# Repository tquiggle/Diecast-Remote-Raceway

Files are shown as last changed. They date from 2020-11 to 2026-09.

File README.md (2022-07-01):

# Diecast-Remote-Raceway
The Diecast Remote Raceway (DRR) allows participants to race 1:64 scale die-cast cars (such as the popular Hot Wheels® cars from 
[Mattel](https://www.mattel.com/en-us)), head-to-head, from remote locations.  A DRR consists of an automated Starting Gate, an electronic Finish Line, and a web service that coordinates races between multiple raceways via the internet.

The DRR is comprised of three components:

* The Starting Gate that manages races on a single track.  The Starting Gate houses a Raspberry Pi Zero W single board computer that performs all local race operations. Reflective infrared track sensors plug into the Starting Gate to signal the presence of a car positioned in each starting location.  A race begins when cars are present in all lanes.  The Starting Gate connects via Bluetoot to the Finish Line that reports when cars finish a race.
* The Finish Line houses an ESP32 Arduino dev board that reports when a car passes over a sensor in each lane.
* The Coordinator is a Node.js application that coordinates the actions of multiple tracks competing against each other.  Each track signals when all lanes have cars ready to race.  When all tracks are ready, the Coordinator signals all tracks to start the local race.  Tracks report the elapsed time for each lane back to the coordinator, which then computes the overall race standings and returns the results to each track to display the race results.

## Operation

Start by mounting the Starting Gate onto a suitable elevated surface. The mount on the bottom of
the Starting Gate can be attached to a [Hot Wheels Clamp
3-way](https://www.thingiverse.com/thing:4037458) to clamp onto a chair, desk, shelf or other
surface.  Alternatively, you can attach to a photography tripod using a [Hot Wheels Track Tripod Connector ](https://www.thingiverse.com/thing:4376073).

Next, attach track sections to build a track of your liking.  Terminate the track with the Finish
Line component.

Apply power to both the Starting Gate and Finish Line using 5 Volt sources
and mini-USB cables.  Most phone chargers or power packs work well to
provide power.  When the Starting Gate has completed its initialization,
the display should look like this:

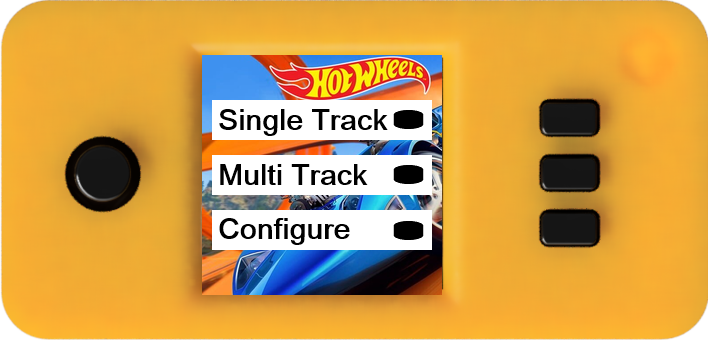
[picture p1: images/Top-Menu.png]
Top Menu


* To race locally, push the top button next to "Single Track"
* To race against another track, push the middle button next to "Multi Track"
* To set configuration parameters such as selecting car icons, other tracks to race against, tack timeout or WiFi parameters, push the button next to "Configure"

Once a race mode has been selected (Single Track or Multi Track) the
Starting Gate will establish a Bluetooth connection to the Finish Line.
This may take a minute or more to complete, during which time the
following is displayed:

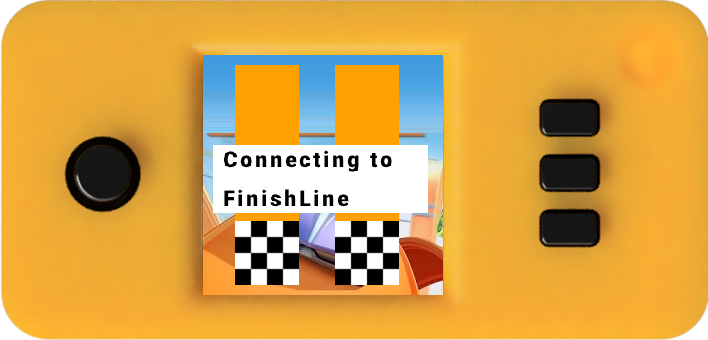
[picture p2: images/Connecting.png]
Connecting


### Multi-Track Race

In a multi-track race was selected, the Starting Gate contacts the race controller to await
another participating track.  The following is displayed:

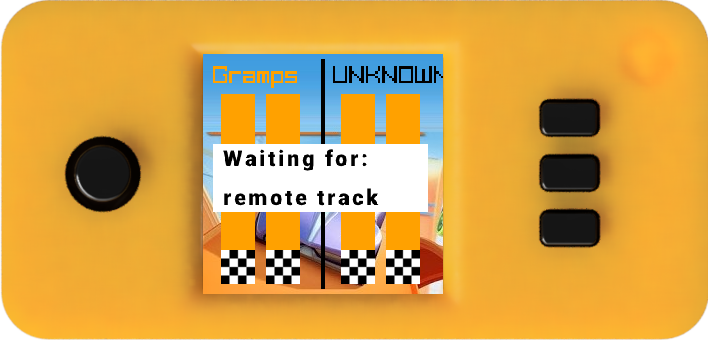
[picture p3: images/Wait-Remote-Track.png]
Wait Remote Track


Upon return, the name of the remote track is displayed
and the Starting Gate awaits cars in each starting gate.

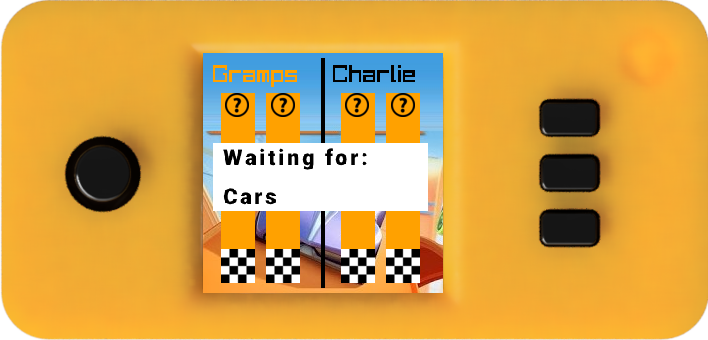
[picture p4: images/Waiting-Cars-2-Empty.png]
Waiting Cars 2


When a lane's sensor detects that a car has been placed in a lane, the "no
car" icon is replaced with the user's selected icon for that lane:

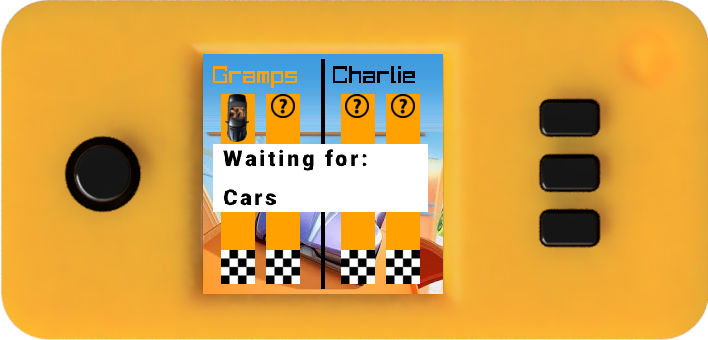
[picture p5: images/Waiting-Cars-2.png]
Waiting Cars 2


Once cars are present in all lanes of the local track the Starting Gate
contacts the race coordinator to signal that the track is ready to race and wait until the
remote track is also ready:

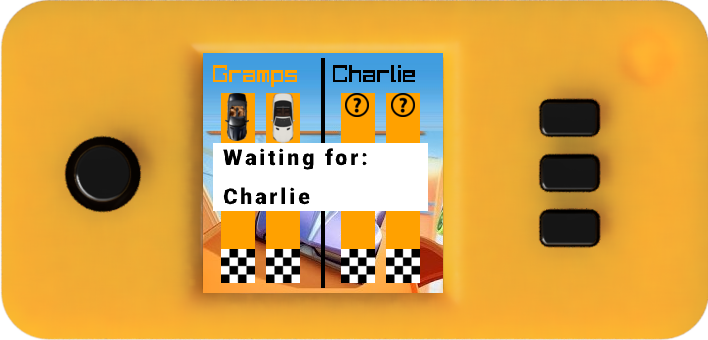
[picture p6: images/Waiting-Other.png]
Waiting on Other Track


Once both tracks are ready, there is a 3 second countdown and the
race begins.  The elapsed time is displayed as the race progresses,
and the icons travel down the image of the track.

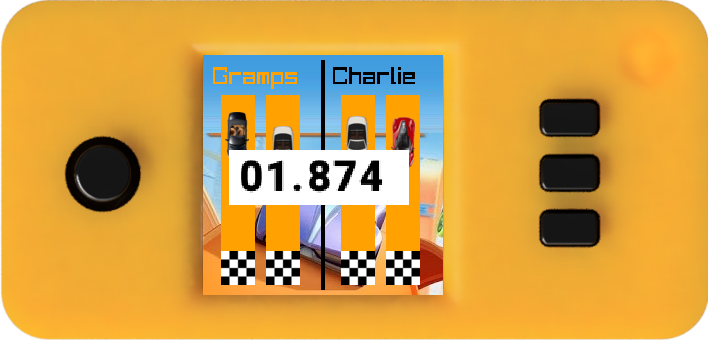
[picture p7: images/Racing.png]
Racing


Finally, when all cars have finished (or the configured timeout is reached) the results of the
race are displayed:

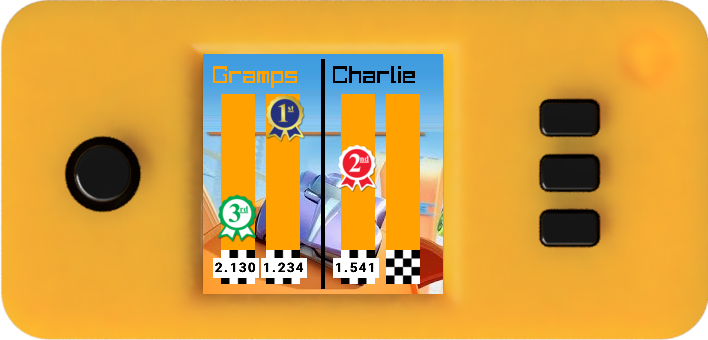
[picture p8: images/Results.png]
Results


and the starting gate barrier is raised to accept cars again.

To start next race, simply placing cars in the gates.  When the first car is placed, the
display clears the race results and goes back to the "Waiting for cars" state and the next race
proceeds.

### Single-Track Race

A Single Track race proceedes much like a Mulit Track but without the coordination with the
second track.  As soon as the connection to the Finish Line is established, the Starting Gate
waits for cars on the local track.

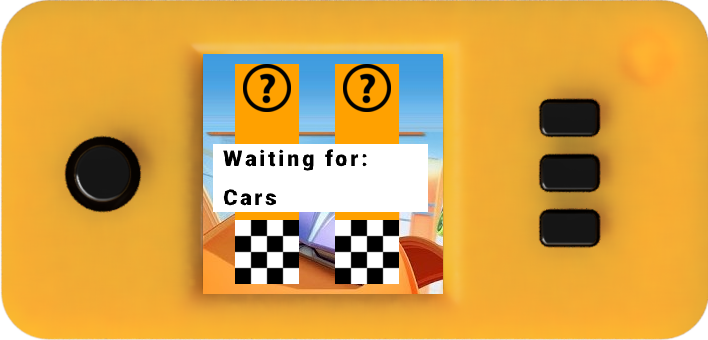
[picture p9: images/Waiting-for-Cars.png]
Waiting for Cars


When a lane's sensor detects that a car has been placed in a lane, the "no
car" icon is replaced with the user's selected icon for that lane:

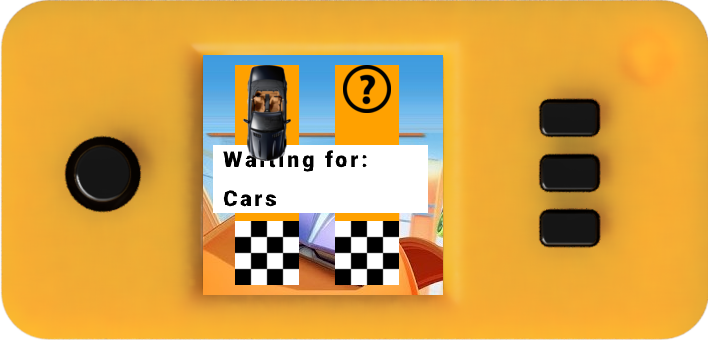
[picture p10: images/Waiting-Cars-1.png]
Waiting with 1 Car


Once all cars are present, there is a 3 second countdown and the race begins.

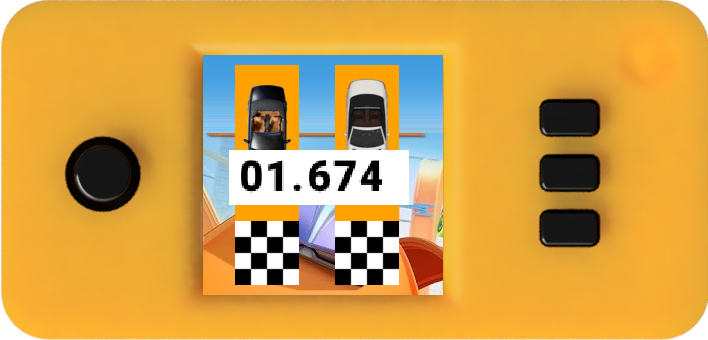
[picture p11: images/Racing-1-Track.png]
Racing 1 Track


When the race completes, the results are displayed:

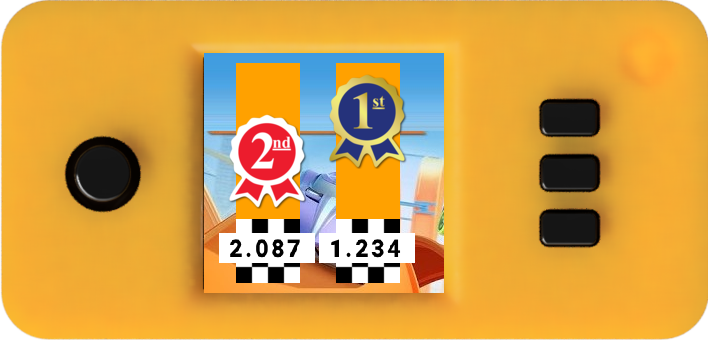
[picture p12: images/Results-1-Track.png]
Racing 1 Track


and the starting gate barrier is raised to accept cars again.

To start next race, simply placing cars in the gates.  When the first car is placed, the
display clears the race results and goes back to the "Waiting for cars" state and the next race
proceeds.

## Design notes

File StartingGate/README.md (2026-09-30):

# Diecast Remote Raceway - Starting Gate

This directory contains the 3D models, software and instructions for the Starting Gate component of the Diecast Remote Raceway.

Starting Gate

## 3D Printed Components

### Starting Gate

The Starting Gate is derived from the excellent design by 
[capsurfer](https://www.thingiverse.com/capsurfer/designs) on 
[Thingiverse](https://www.thingiverse.com/thing:4026846) with a number of modifications to adapt it to automation.

The following components are printed exactly as-is from capsurfer's original design:

* connector_v2.stl
* lever.stl
* lid.stl
* starter.stl
* thestick[\_long4].stl

As they are capsurfer's unmodified designs, I have not included the STL files in this
repository.  You will need to download those STLs from thingiverse.

The following components have been modified to suit automation

* open-box.stl - a modified version of box.stl to insert the track with a mounted sensor from the back of the box. The sensor would collide with the starter if inserted from the front.
* open-box-servo.stl - a modified version of open-box.stl for Lane 1 with an opening and mounting holes for a MG90S servo.
* sensor-track.stl - a modified version of track.stl designed to mount a [TCRT5000 Infrared Reflective Sensor Module](https://www.amazon.com/gp/product/B081RPJ44L) to detect the presence of a car.

* sensor-track-flush.stl - a modified version of sensor-track.stl that moves the sensor forward about 10mm.  Requires reworking the TCRT5000 sensors. See note below.
* servo-knob.stl - Modified version of knob.stl to make the arm much narrower and add holes for the servo control.
* lane-#.stl - modified versions of sensor-track-flush.stl with embossed lane numbers

I also moved the location of the track extrusions that accept the threaded heat set screw inserts further away from the track surface to
eliminate bulging of the track surface. This required changes to both the open-box\* and
sensor-track\* relative to the original they are derived from.

New components added to the design:

* back-lid.stl - a removable lid on the back of the box that secures the track.
* mount.stl - a mount that attaches to the bottom of a box allowing the box to be mounted on a [Hot Wheels Clamp 3-way](https://www.thingiverse.com/thing:4037458) or a [Hot Wheels Track Tripod Connector ](https://www.thingiverse.com/thing:4376073).

#### Note on Track Sensors
With an unmodified IR sensor, the sensor needs to be mounted entirely aft of the starter which leaves very little room for the wiring and puts the sensor at the back bumper of shorter cars.

By reworking the TCRT5000 IR Sensor to mount the LED/Photosensor pair flush with the PCB, the sensor module can be moved forward about 10mm
giving more room for wiring and a better sensing location.  This requires desoldering the LED/Photosensor, clipping the plastic stand-offs
and resoldering the LED and Photosensor after repositioning.  If you aren't comfortable desoldering the LED/Photosensor components, just print the
sensor-track.stl. I felt the relocation was worth the effort of reworking the sensor modules.  I found this inexpensive
[Vacuum Desoldering Iron](https://www.jameco.com/z/VTDESOL3U-Velleman-10-5-Long-Vacuum-Desoldering-Pump-with-30W-Heater-Yellow-_2131021.html)
made the job easy.

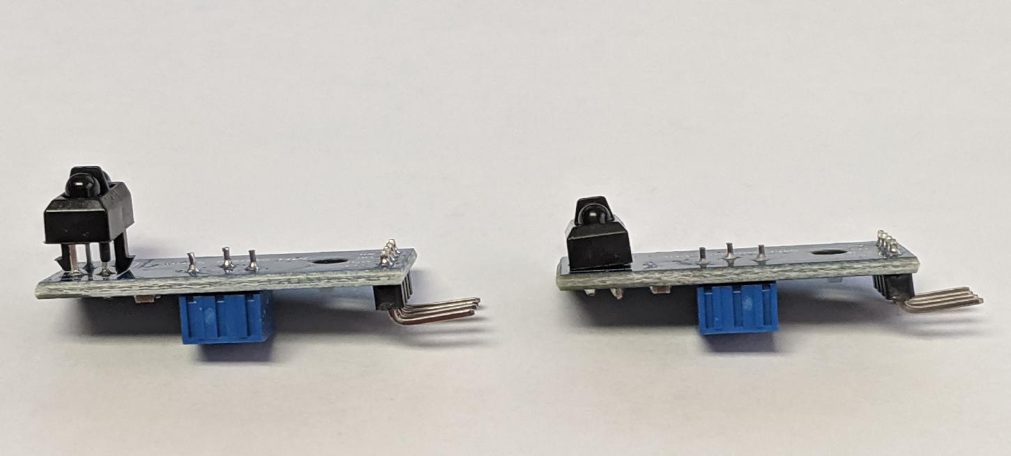
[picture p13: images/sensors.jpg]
IR Sensors


An unmodified sensor is shown on the left and a reworked sensor on the right.

#### License

To conform to capsurfer's licensing for the Starter Box from which these components are
derived, the Starting Gate components are released under the [Creative Commons
Attribution - NonCommercial - ShareAlike](https://creativecommons.org/licenses/by-nc-sa/4.0/) license.

### Controller

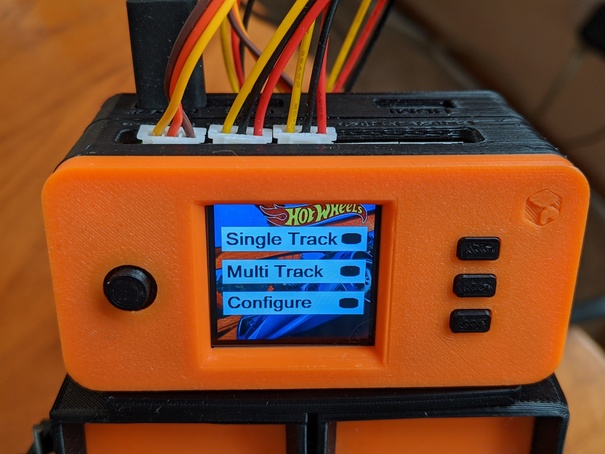
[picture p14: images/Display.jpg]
Display


The control hardware is housed in a three piece case that is based on [JdaieLin](https://github.com/JdaieLin)'s [PiSugar Case](https://github.com/PiSugar/PiSugar).  The controller consists of four 3D printed components:

* bottom-cover.stl - this is an optional bottom cap for use on a completed controller case 
while testing, before mounting to a set of starting gate lanes.  It is based on the PiSugar [pisugar_case_common_cap.STL](https://github.com/PiSugar/PiSugar/blob/master/model/pisugar_case_common_cap.STL) but has been modified to slightly beef up the clips that hold the cap onto the bottom of the pi-zero-case.
* pi-zero-case.stl - a modified version of PiSugar's
[pisugar_nobatt_shell.STL](https://github.com/PiSugar/PiSugar/blob/master/model/pisugar_nobatt_shell.STL) with embossed labels for the exposed ports. The Raspberry Pi Zero board mounts to this case.
* connector-case.stl - case for the Prototyping pHAT or custom PCB with JST connectors. Snaps onto the
pi-zero-case.
* lcd-cap.stl - a slightly modified version of the PiSugar 
[1.3inch_lcd_cap](https://github.com/PiSugar/pisugar-case-pihat-cap/blob/master/1.3inch_lcd_cap/pisugar_case_lcd_cap.STL)
with fillets to beef up the clips.  You will need to print the buttons and joystick cap from
the original design. The file is
[pisugar_case_lcd_button_comp.STL](https://github.com/PiSugar/pisugar-case-pihat-cap/blob/master/1.3inch_lcd_cap/pisugar_case_lcd_button_comp.STL).

* mount.stl - a bracket that screws to the back of lanes 1 & 2 and holds the controller case. The controller snaps onto the mount.

#### License

To conform to [JdaieLin](https://github.com/JdaieLin)'s 
licensing for the PiSugar from which these components are
derived, the Controller case components are released under the 
[GNU General Public License v3.0](https://www.gnu.org/licenses/gpl-3.0.en.html).

## Hardware

The Controller electronics is comprised of a stack of 3 circuit boards: a Raspberry Pi Zero W (or Zero 2 W), a custom Connector Breakout Board that the servo and lane sensors plug into, and a Waveshare 1.3" LCD Hat for input and display.

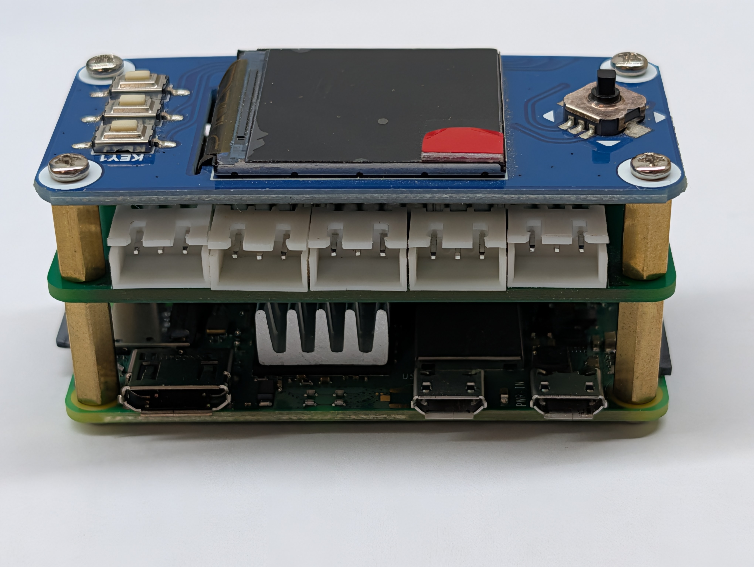
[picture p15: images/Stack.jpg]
Stackzero


### Raspberry Pi Zero

The Starting Gate is controlled by a Raspberry Pi Zero W (or Zero 2 W).  These are normally available for about $15 without the GPIO header or about
$20 for the WH model with preinstalled GPIO headers.  However with the current AI hardware boom, Raspberry Pi Holdings is experiencing supply chain
issues and as of Fall 2026 boards are extremely hard to get.

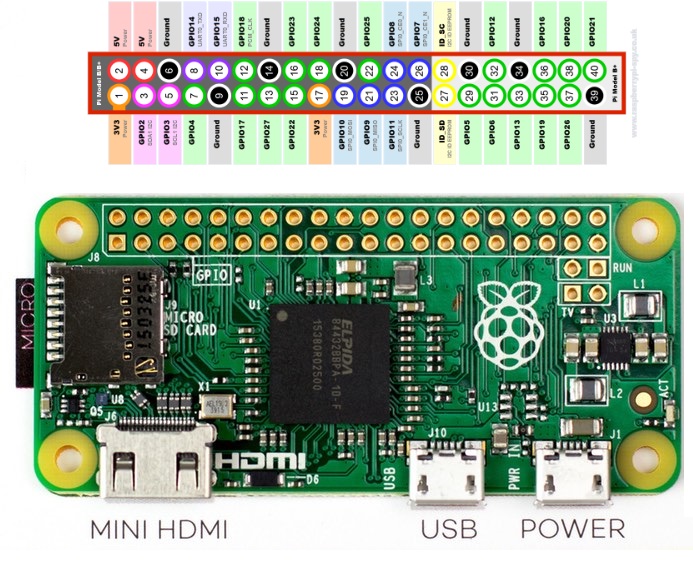
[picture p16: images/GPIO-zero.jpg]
GPIO-zero


#### GPIO Usage

| SYMBOL | BROADCOM GPIO (BCM) | RASPBERRY PI PIN | DESCRIPTION |
|:---:|:---:|:---:|:---:|
| KEY1 | GPIO21 | 40 | Button 1/GPIO |
| KEY2 | GPIO20 | 38 | Button 2/GPIO |
| KEY3 | GPIO16 | 36 | Button 3/GPIO |
| Joystick Up | GPIO6 | 31 | Joystick Up |
| Joystick Down | GPIO19 | 35 | Joystick Down |
| Joystick Left | GPIO5 | 29 | Joystick Left |
| Joystick Right | GPIO26 | 37 | Joystick Right |
| Joystick Press | GPIO13 | 33 | Joystick Press |
| SCLK | GPIO11/SCLK | 23 | SPI clock input |
| MOSI | GPIO10/MOSI | 19 | SPI data input |
| DC | GPIO25 | 22 | Data/Command selection (high for data, low for command) |
| CS | GPIO8/CE0 | 24 | Chip selection, low active |
| RST | GPIO27 | 13 | Reset, low active |
| BL | GPIO24 | 18 | Backlight |
| Servo | GPIO12 (PWM0) | 32 | Servo |
| LANE1 | GPIO7 | 26 | Lane 1 Sensor |
| LANE2 | GPIO23 | 16 | Lane 2 Sensor |
| LANE3 | GPIO22 | 15 | Lane 3 Sensor |
| LANE4 | GPIO4 | 7 | Lane 4 Sensor |

### Connector Breakout Board

The Connector Breakout Board (CBB) connects to the Raspberry Pi
GPIO connector and provides JST connectors to plug in the servo and
lane sensors. There are two options for the CBB: use a commercially
available ModMyPi Zero Prototyping pHat and solder jumper wires to
create the necessary circuit, or use the provided Gerber files to
have a custom PCB printed. The PCB solution involves less soldering
and is cleaner, but requires you to have the PCBs fabricated.  I used
[PCBWay](https://www.pcbway.com/).

#### Prototyping pHAT Schematic

Connections to the car release servo and lane car sensors
are made via JST connectors soldered to a [ModMyPi Zero Prototyping
pHAT.](https://www.pishop.us/product/zero-prototyping-phat-zero/). The
schematic is shown below.

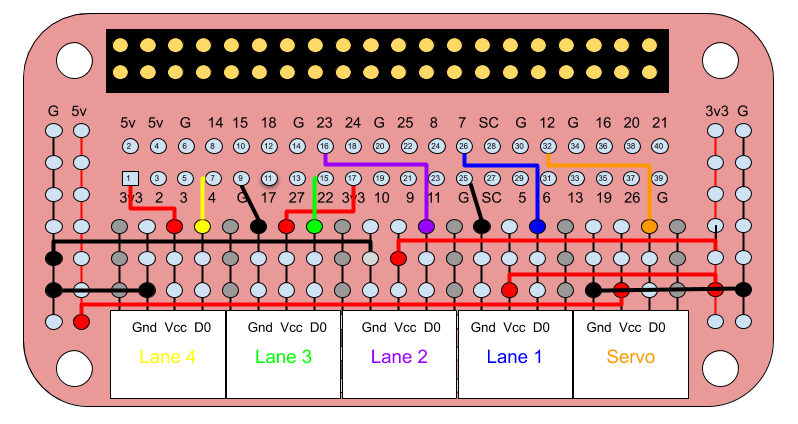
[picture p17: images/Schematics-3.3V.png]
pHAT-Schematics


#### Custom PCB

The Gerber files for the CBB HAT can be found in the gerber folder.  Alternately, you can order a set of 5 boards for $5 (plus
shipping) directly from PCBWay. 
[Diecast Remote Raceway - Connector Breakout Board HAT](https://www.pcbway.com/project/shareproject/Diecast_Remote_Raceway_Connector_Breakout_Board_HAT_055c51ce.html)

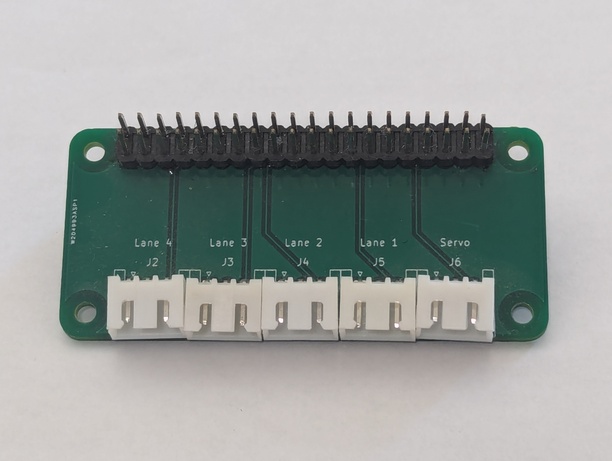
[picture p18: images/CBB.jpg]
CBB


### Waveshare 1.3" LED HAT

The Waveshare 1.3" LCD HAT provide three button input and a joystick for navigation.  The race state and results are shown on the display.

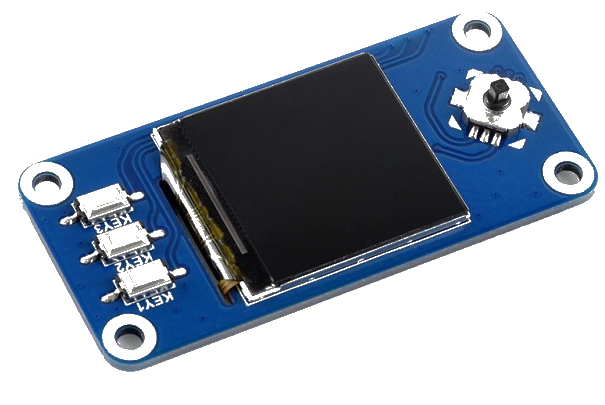
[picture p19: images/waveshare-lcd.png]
LCD HAT


## Software

The Starting Gate consists of the following components

* config.py manages configuration settings
* coordinator.py interface to the Race Coordinator server when running multi-track races
* deviceio.py interface to WaveShare 1.3" LCD buttons, servo and GPIO PINs for sensing cars
* display.py manages the race display
* drr\_wrapper.py called from /etc/rc.init at boot, checks for software updates and runs starting\_gate.py as a child process.  If starting\_gate.py fails for any reason, it is restarted
* finishline.py manages communication with the Finish Line
* input.py accepts user input via character selection from a grid
* menu.py manages the top level menu and all configuration menus
* starting\_gate.py is the executable for the starting gate. It displays the initial menu and runs races
* wifi.py  is responsible for managing the WiFi interface

## Raspberry Pi Software Setup

### Using Raspberry Pi Imager

The easiest way to get up and running is to use a preconfigured OS image
from the DRR GitHub repository.

The image contains a Raspberry Pi OS Lite with the necessary drivers, libraries,
DRR software and user account already installed. Two images are available, one
for the Raspberry Pi Zero W and one for the Raspberry Pi Zero 2 W.
The former is 32 bit and the latter 64 bit.

The image can be installed directly using the 
[Raspberry Pi Imager](https://www.raspberrypi.com/software/).
Download and install the latest version.

By default, the Raspberry Pi Imager will not customize a bare downloaded image file.  You will
need to use a custom Content Repository.

Run the Raspberry Pi Imager and configure to use custom OS image as follows:

1.  Click the  "APP OPTIONS" button
1.  Click the "EDIT" button after Content Repository
1.  Select "Use custom URL"
1.  Copy and Paste the following URL into the text box:

```bash
    https://raw.githubusercontent.com/tquiggle/Diecast-Remote-Raceway/refs/heads/master/StartingGate/util/drr_repo.json
```

5.  Click "APPLY & RESTART"

Insert the card into an appropriate card reader on your computer, or in a 
[USB SD Card Reader](https://www.amazon.com/dp/B0DQ71G4G4?th=1).

Select the Zero board you are using. The correct OS image should be the only option in the OS menu.

In the OS image, the Hostname is pre-configured as 'drr' and the
user 'drr' has been created with the password "HotWheels".  In the
Customisation menu, just click 'NEXT' to skip these.  NOTE: If you create
a new user, it will REPLACE the drr user and the startup process will
fail when it can't find the '/home/drr' directory!

When the image is done writing and verifying, remove the microSD chip and insert it into your controller.  On the first
startup, it will expand the filesystem to the size of your SD card.  Subsequent startups should be a bit quicker.

#### Building from Scratch

See the file master-install.sh in the StartingGate/util directory for details on how to build an image from scratch.
Running the script on a fresh Raspberry Pi installation will create a working Starting Gate system.

### Configuring WiFi

If you know the credentials of the WiFi network that your Diecast Remote Raceway components will connect to, simply
configure the SSID and password when burning the image with the Raspberry Pi Imager.  Otherwise there are two
options to configure later

#### Using the Starting Gate Hotspot

When the Starting Gate boots, if it can not connect to WiFi it starts a WiFi Hotspot named 'DRR WiFi Setup'
Simply connect to this WiFi Hotspot using your phone/tablet/laptop. There is no password. Once connected 
you will be directed to a captive portal page to select a WiFi network and enter the password.

#### Using the Starting Gate configuration menu

From the top level menu, push the bottom button to enter the configuration menu.  From there,
select "WiFi Setup" and fill in the WiFi region (if necessary) and the SSID and Password.

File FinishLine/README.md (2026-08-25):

# Diecast Remote Raceway - Finish Line

This folder contains the 3D models, software and instructions for the
Finish Line component of the Diecast Remote Raceway.

## 3D Printed Components

### Finish Lanes

The Finish Lane design is derived from the Starting Box design by 
[capsurfer](https://www.thingiverse.com/capsurfer/about) on 
[Thingiverse](https://www.thingiverse.com/thing:4026846).  His sketch for
the profile of the track was re-used as the basis for the profile
for the finish line.  The cut-outs for the track connectors are similarly
based on capsurfer's sketches in his original Fusion360 design.  All other
aspects are my own creation.

* Controller-Box.stl - Box to house the ESP32 development board and Infrared Tracking Sensor Module
* Controller-Lid.stl - Solid lid to Controller-Box
* Controller-Lid-Adjust.stl - Controller-Box lid with viewing window and access holes for adjusting sensitivity
* Track-1.stl - Finish line for lane 1
* Track-2.stl - Finish line for lane 2
* Track-3.stl - Finish line for lane 3
* Track-4.stl - Finish line for lane 4
* Track-Bottom-Cover.stl - Snap-on cover for wiring on lane

#### License

Since I started with a sketch from capsurfer's Starter Box, the Starting Gate components are released under 
the same [Creative Commons Attribution - NonCommercial - ShareAlike](https://creativecommons.org/licenses/by-nc-sa/4.0/) license.

## Hardware

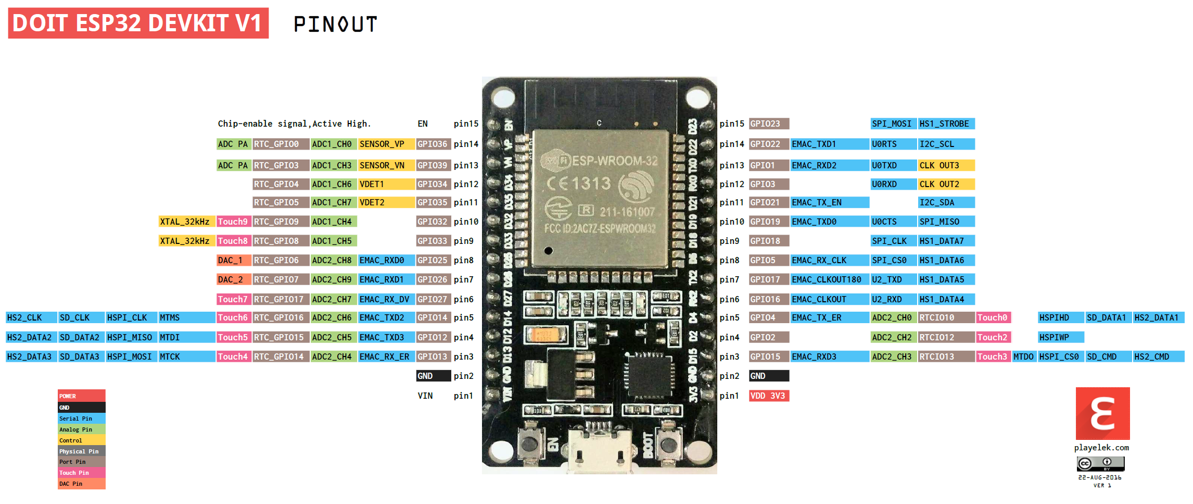
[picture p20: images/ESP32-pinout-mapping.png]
ESP32 devkit


The wiring to connect the ESP32 dev board to the YWBL-WH Infrared Tracking Sensor Module is shown below:

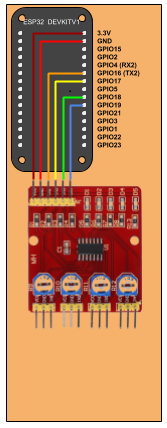
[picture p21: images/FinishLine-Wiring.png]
Finish Line Wiring


I used a 6 pin Dupont connector for the YWBL-WH header and two right angle crimp-on connectors to connect to
the ESP32. The ribbon cable was split to accommodate two right angle connectors: a two pin connector for Vcc and
GND, and a *5 pin* connector to connect the four lane sensors to GPIO16 through GPIO19.  Note that the middle
pin of the 5 pin connector that would connect to GPIO05 is not connected.

### Lane Sensitivity Adjustment
The Starting Gate and Finish Line detect cars by infrared light reflected off the bottom of the car.  As such,
they are sensitive to ambient infrared light striking the sensor.  If the sensors are exposed to high levels of
ambient infrared lighting, such as in direct sunlight, they may report a car when none is present.  The
sensitivity of each Finish Line can be adjusted.

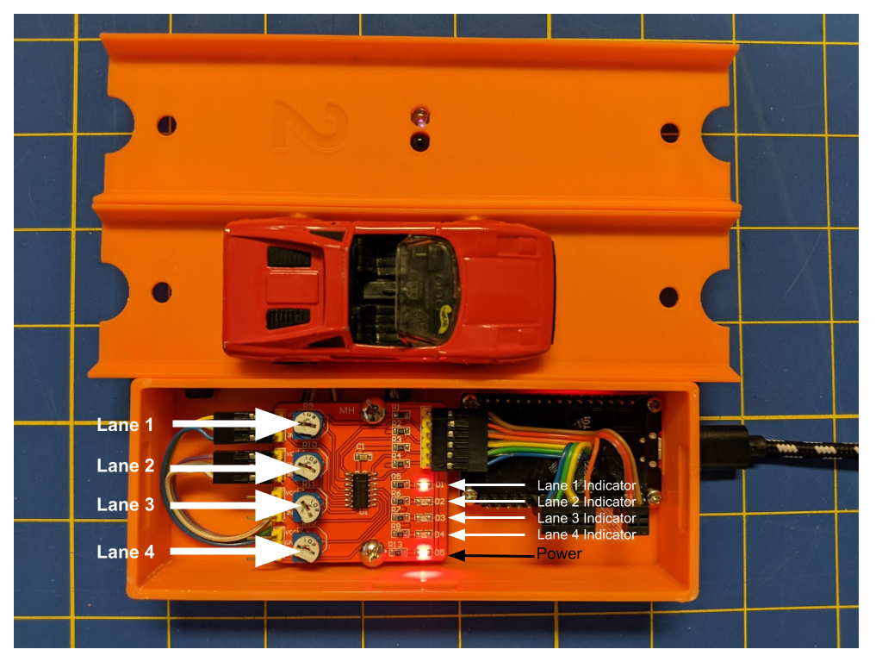
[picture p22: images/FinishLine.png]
Finish Line


The LED labeled “D5” is a power indicator.  It will illuminate whenever power is applied to the Finish Line.

Adjustments are made with a small screwdriver using the four trim potentiometers labeled “Lane 1” through
“Lane4” in the above photo.  When correctly adjusted, the lane indicator LED will be unlit when no car is
present in a lane and will light up when a car is placed over the sensor.  To adjust, make sure the Finish Line
is plugged into a 5V power source.  Start with no car present.  Turn the white potentiometer corresponding to
the lane until the indicator lights up.  Then turn back just past the point where the light turns off.  Test the
lane by placing a car over the sensor.  The corresponding indicator should illuminate.

## Software Updates

In the initial implementation, the Finish Line checked for software updates on every restart.  This required
bringing up the WiFi interface, connecting using a SSID and password stored in config, fetching the most recent
release version number and comparing it to the version running.  If a newer version was available, it would be
downloaded and run.

This had two problems.  First, it unnecessarily brought up the WiFi interface and lengthened the
(already too long) startup time even when there was no software update. Second, it required
storing a fair amount of configuration data in SPIFFS that is difficult to update.  While you CAN
set config values over bluetooth using the SETC command, it's not exactly convenient. If setting
the WiFi config values, it would send the WiFi password unencrypted over Bluetooth - something I'm
loath to do!

The update check has since been moved to the Starting Gate. If the Starting Gate has a WiFi
connection, once it has established a Bluetooth connection to the Finish Line, it sends a FLVS
command to retrieve the Finish Line Version String. The Starting Gate then checks if an update
is available.  If so, it sends a UPFW command to the Finish Line telling it to update its firmware.
The UPFW command passes a JSON argument containing the WiFi SSID, an encrypted password/pks
string and the URL of the updated software image.

In order to encrypt the WiFi password, the Starting Gate requests a RSA public key
from the Finish Line via the GKEY command.  In response to the GKEY command, the Finish Line generates
a 2048 bit random RSA key pair and returns the public key in PEM format. The Starting Gate uses this
public key to encrypt the WiFi password before sending it as part of the JSON argument to the
UPFW command.

The only remaining configuration variable maintained in SPIFFS is the Bluetooth advertisement
string which defaults to "FinishLine".  The only reason to change this value is if you are
running multitrack races where both tracks are connected to the same WiFi. I did this
extensively when developing the software. For example, if you wanted to set the Bluetooth
advertisement on a Finish Line to "FinishLine2," you can use the sendcmd.py script in the 
StartingGate's 'util' directory:

```console

% ./sendcmd.py 'SETC bluetoothAdvertisement=FinishLine2'

```

and update the corresponding FINISH\_LINE\_NAME config in the Starting Gate that you want
to connect to the Finish Line.

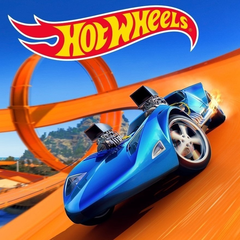
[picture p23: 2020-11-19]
StartingGate/images/background-2.png

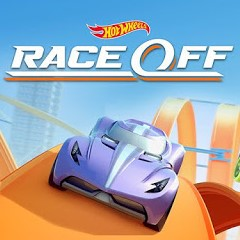
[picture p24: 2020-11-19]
StartingGate/images/raceoff.png

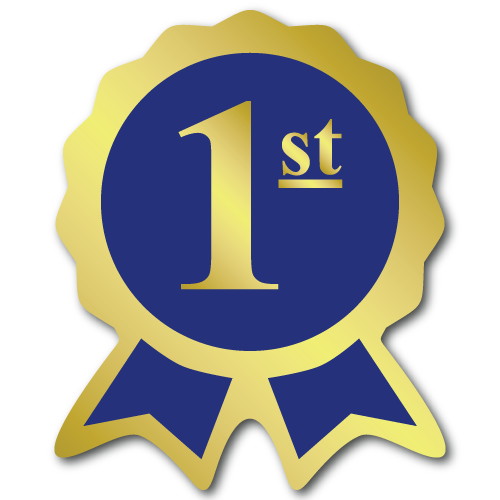
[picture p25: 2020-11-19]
StartingGate/images/1st-orig.png

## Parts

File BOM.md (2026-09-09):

# Bill Of Materials 

## US Suppliers

This is a list of parts from US suppliers with < 1 week shpping times.
These are (mostly) the exact SKUs I purchased when designing and building
the raceway.  Prices are accurate as of when I ordered the, but may have
changes since.  In many cases, I purchased kits with multiple connectors
or parts to experiment with.  Not counting "consumables" like screws,
nuts, wire and wiring connectors, two 4-lane tracks can be built with
readily availale parts for about $150.  If you're willing to wait for
shipping from China, you could obtain the same parts for under $90.
All prices include shipping, but not taxes. Note: I'm an Amazon Prime
member, non Prime members may incur additional shipping costs."

### Update September 2026

Due to RAMageddon driven by demand for AI computing, the Raspberry Pi Zero family is increasingly difficult to source.  Both the original Raspberry Pi Zero W and the newer
Raspberry Pi Zero 2 W will run the Starting Gate fine.  You can't tell the difference in performance during a race. Go with whatever board you can find.  As of this writing, the
original Raspberry Pi Zero W is in stock at the following:

https://www.waveshare.com/raspberry-pi-zero-w.htm?sku=14298

https://www.seeedstudio.com/Raspberry-Pi-Zero-WH-p-4401.html

| Item | # | Each | Total | Vendor |
| :--- | :--- | ---: | ---:  | :--- |
| **Starting Gates** | |  |  |  |
| Raspberry Pi Zero 2 W with Header| 2 | $18.00 | $36.00 | <span style="color:red">https://www.pishop.us/product/raspberry-pi-zero-wireless-wh-pre-soldered-header/</span> |
| or | | | | |
| Raspberry Pi Zero W[H] | 2 | $16.00 | $32.00 | <span style="color:red">https://www.pishop.us/product/raspberry-pi-zero-wireless-wh-pre-soldered-header/</span> |
| 1.3" LCD Display Hat | 2 | $18.23 | $36.46 | https://www.amazon.com/1-3inch-LCD-Display-HAT-IPS/dp/B07VJ8G6SX?th=1 |
| Zero Prototyping pHAT | 2 | $5.45 | $10.90 | https://www.pishop.us/product/zero-prototyping-phat-zero/ |
| or | | | | |
| Conector Breakout Board PCB| 2 | (5 for $5.00) + S&H | $11.30 | https://www.pcbway.com/project/shareproject/Diecast_Remote_Raceway_Connector_Breakout_Board_HAT_055c51ce.html |
| TCRT5000  IR Reflective Sensor Modules | 8 | (10 for $7.99) | $7.99 | https://www.amazon.com/ACEIRMC-TCRT5000-Reflective-Photoelectric-Avoidance/dp/B08YRCR6ML/ |
| MG90S Servo | 2 | (2 for 9.99) | $9.99 | https://www.amazon.com/Maxmoral-Upgraded-Digital-Vehicle-Helicopter/dp/B07NV476P7 |
| JST XH 2.54mm 3-pin connectors| 10 | (50 for 7.19) | $7.19 | https://www.amazon.com/dp/B0BMDZR7RZ?th=1 |
| 40 pin (20x2) GPIO Stacking Header | 2 | (assortment for $9.90) | $9.90 | https://www.amazon.com/dp/B0827THC7R |
| **Finish Lines** | |  |  |  |
| ESP32 ESP-32S Development Board  | 2 | (2 for 14.89) | $12.99 | https://www.amazon.com/dp/B09XDMVS9N/ |
| 4-Channel IR Line Tracking Sensor Module | 2 | $6.39 | $12.78 | https://www.amazon.com/dp/B07Q2HRXN4 |
| 2.54 MM Right Angled IDC Receptacle - 2 Position | 2 | $0.54 | $1.08 | https://www.digikey.com/en/products/detail/w-rth-elektronik/661002152222/10239727 |
| 2.54 MM Right Angled IDC Receptacle - 5 Position | 2 | $0.77 | $1.54 | https://www.digikey.com/en/products/detail/w-rth-elektronik/661005152222/10239742 |
| IDC Receptacle Shipping | | 4.99  | $4.99 | |
| **Assembly** | |  |  |  |
| M4-0.7 Metal Threaded Heat Set Screw Inserts | 1 | 9.99 | 9.99 | https://www.amazon.com//dp/B0FGCX5XT4/ |
| M4 x 0.7mm SS Nylon Lock Nuts | 1 | 4.99  | $4.99 | https://www.amazon.com/gp/product/B075ZZD3NN |
| M4 x 0.7 x 10 SS Flat Head Socket Cap Screws | 1 | 6.99 | $6.99 | https://www.amazon.com/dp/B0CPSFJDRY |
| M4 x 0.7 x 10 SS Allen Head Socket Cap Screws | 1 | 8.05 | $8.05 | https://www.amazon.com/dp/B0DCK5GW5F?th=1 |
| M2.5x14 Brass MF Standoff 20pc | 1 | 6.79 | 6.79 | https://www.amazon.com/dp/B0F18F47Z4/ |
| M2.5x10 Brass FF Standoff 50pc | 1 | 9.99 | 9.99 | https://www.amazon.com/dp/B08F1W3ZXW |
| **Tools and Wiring** | | | |
| Crimping Tool Kit w/ Dupont & JST-XH Connectors | 1 |  | $29.99 | https://www.amazon.com/gp/product/B07ZK5F8HP |
| SN-01BM Crimping Tool | 1 |  | $22.99 | https://www.amazon.com/gp/product/B00YGLKBSK |
| 10 feet ribbon cable | 1 |  | $6.86 | https://www.amazon.com/gp/product/B007R9SQQM |

## Cost Optimized

Needs updating...

| Item | # | Each | Total | Vendor |
| :--- | :--- | ---: | ---:  | :--- |
| **Starting Gates** | |  |  |  |
| Raspberry Pi Zero W[H] | 2 | $14.95 | $29.90 | https://www.pishop.us/product/raspberry-pi-zero-wireless-wh-pre-soldered-header/ |
| 1.3" LCD Display Hat | 2 | 13.50  | 27.00  | https://www.ebay.com/itm/384341552873 |
| Zero Prototyping pHAT | 2 | $6.95 | $13.90 | https://www.pishop.us/product/zero-prototyping-phat-zero/ |
| TCRT5000  IR Reflective Sensor Modules | 8 | (8 @ $0.40 + $2.61 shipping) | $5.81 | https://www.aliexpress.com/item/1005001841063508.html |
| MG90S Servo | 2 | (2 @ 1.39  2.47 shipping) | $5.52 | https://www.aliexpress.com/item/1005002071884212.html |
| **Finish Lines** | |  |  |  |
| ESP32 ESP-32S Development Board  | 2 | (2 for 9.69) | $9.69 | https://www.aliexpress.com/item/32864722159.html |
| 4-Channel IR Line Tracking Sensor Module | 2 | | $2.94 | https://www.aliexpress.com/item/33007862609.html |

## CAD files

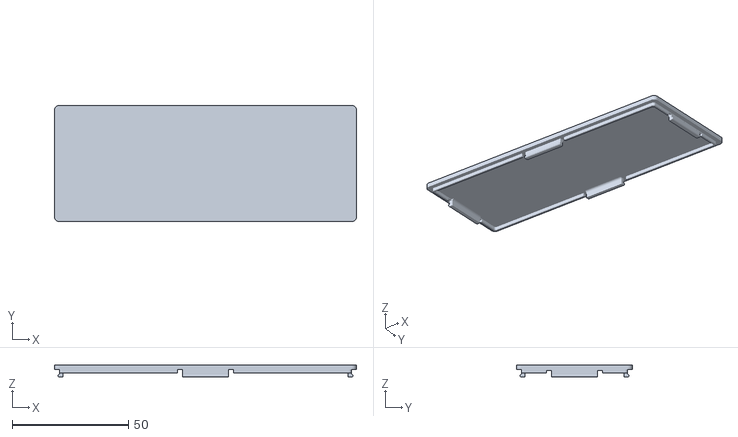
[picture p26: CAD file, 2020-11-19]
FinishLine/STL/Controller-Lid.stl
130.0 x 50.0 x 5.26

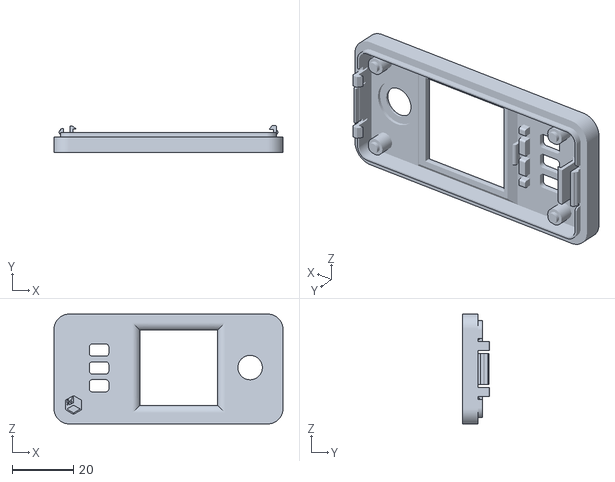
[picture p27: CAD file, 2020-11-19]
StartingGate/STL/controller/lcd-cap.stl
75.0 x 8.80 x 36.0

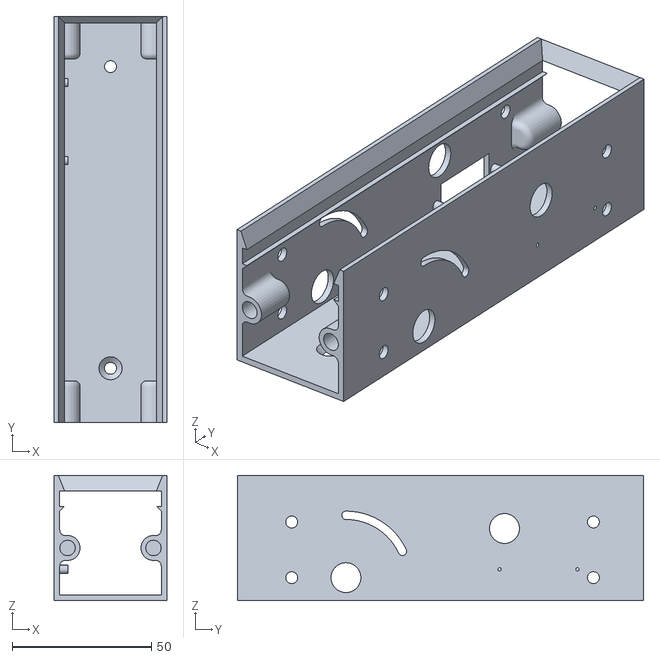
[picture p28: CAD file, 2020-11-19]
StartingGate/STL/starter_box/open-box-servo.stl
40.5 x 146.0 x 45.0

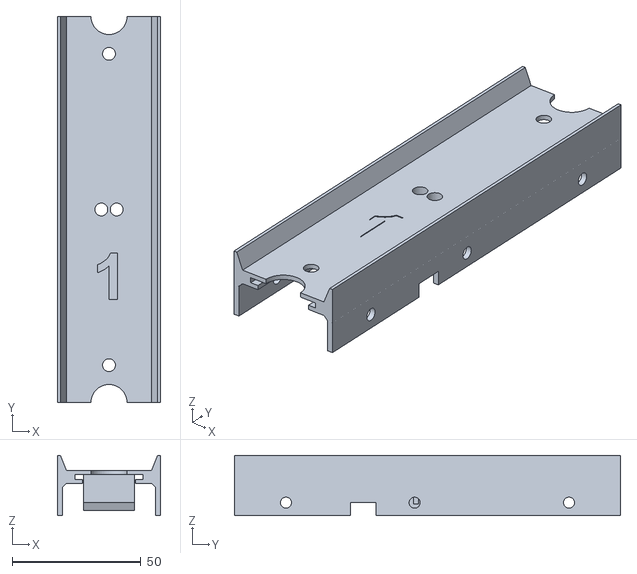
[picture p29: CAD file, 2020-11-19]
FinishLine/STL/Track-1.stl
40.0 x 150.0 x 23.3

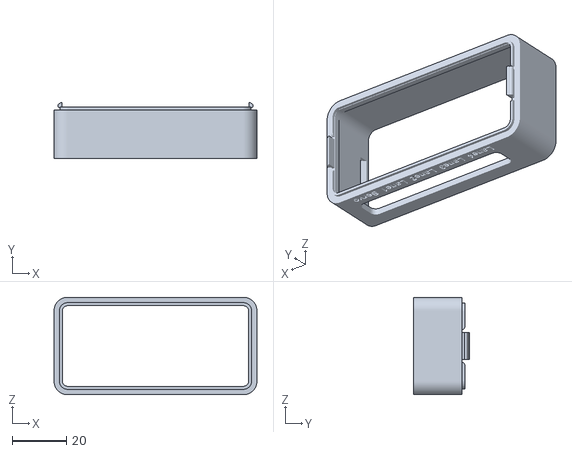
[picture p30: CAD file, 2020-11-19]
StartingGate/STL/controller/connector-case.stl
75.0 x 20.8 x 36.0

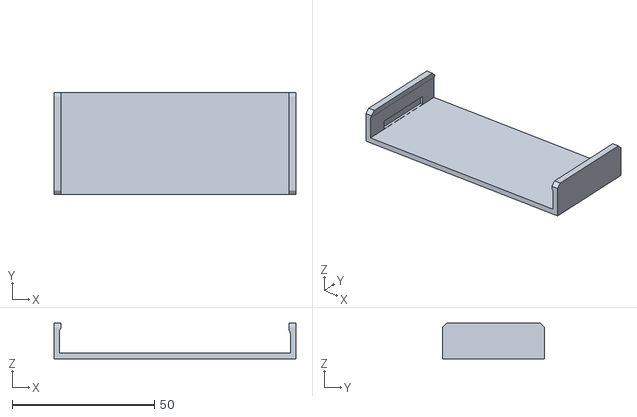
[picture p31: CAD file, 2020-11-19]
FinishLine/STL/Track-Bottom-Cover.stl
85.0 x 36.0 x 12.6

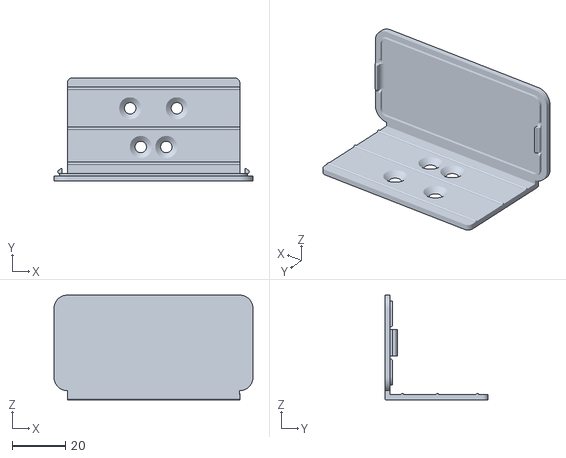
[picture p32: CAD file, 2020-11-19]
StartingGate/STL/controller/mount.stl
75.0 x 39.0 x 39.5

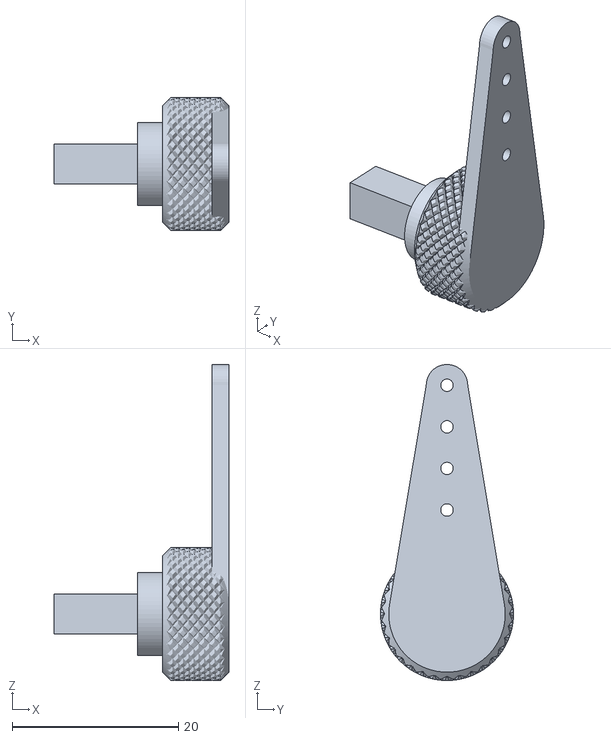
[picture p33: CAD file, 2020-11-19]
StartingGate/STL/starter_box/servo-knob.stl
21.0 x 16.0 x 38.0

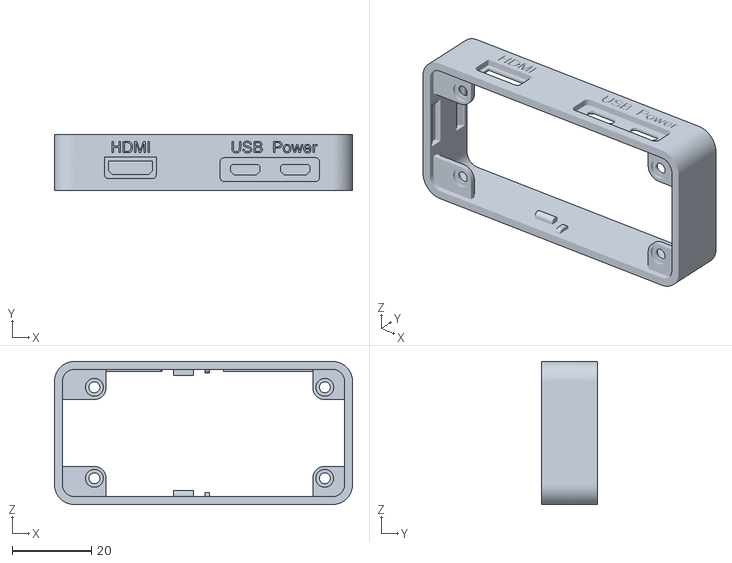
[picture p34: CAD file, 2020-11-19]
StartingGate/STL/controller/pi-zero-case.stl
75.0 x 14.0 x 36.0

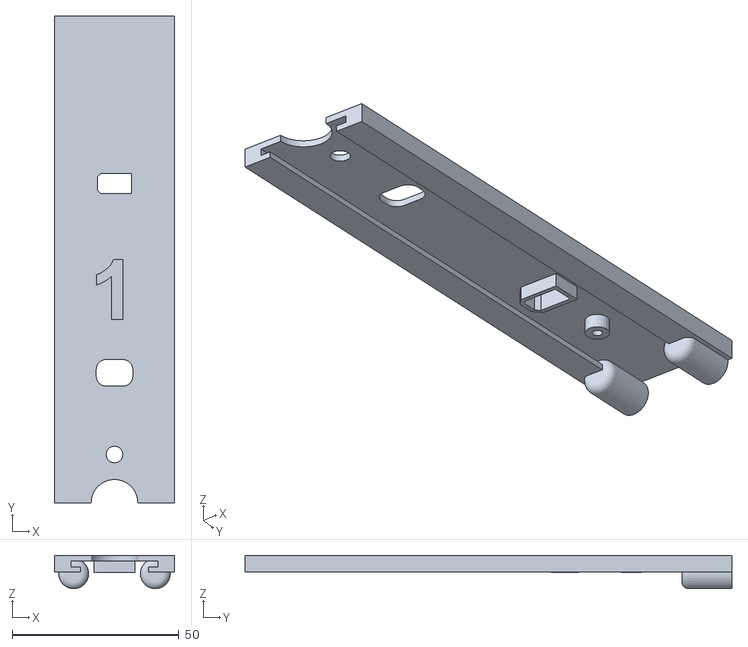
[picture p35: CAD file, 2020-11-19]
StartingGate/STL/starter_box/lane-1.stl
36.0 x 146.0 x 9.99

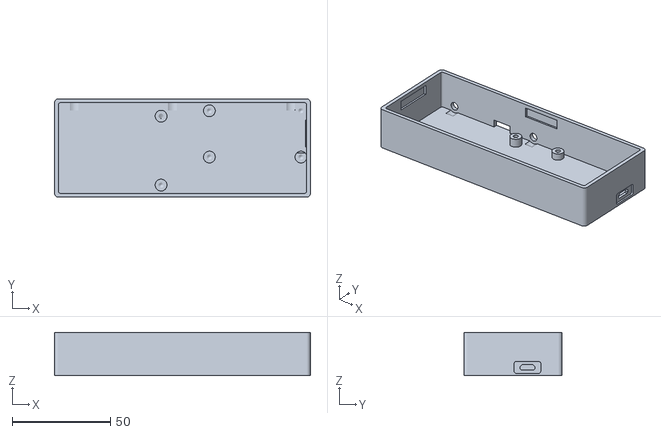
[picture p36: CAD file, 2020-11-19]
FinishLine/STL/Controller-Box.stl
130.0 x 50.0 x 22.0

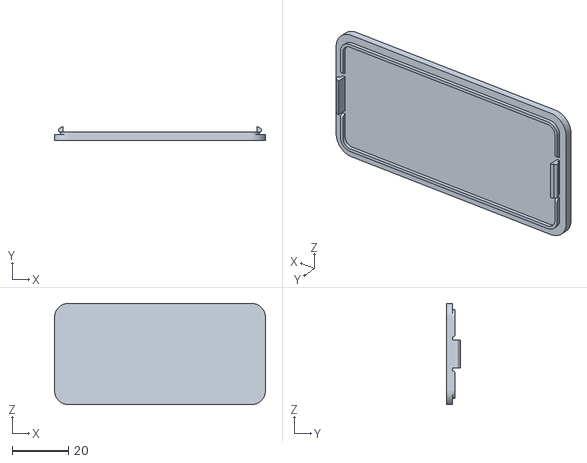
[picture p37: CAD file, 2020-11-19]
StartingGate/STL/controller/bottom-cover.stl
75.0 x 4.80 x 36.0

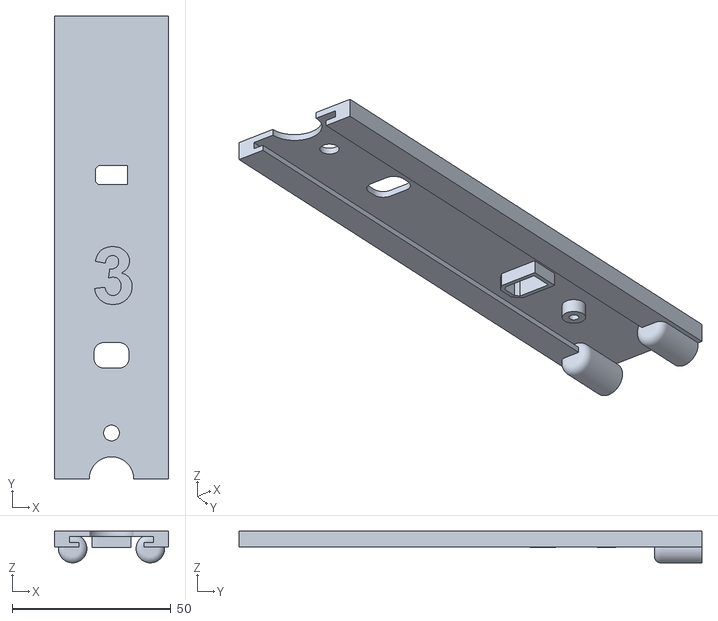
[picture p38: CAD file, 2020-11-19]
StartingGate/STL/starter_box/lane-3.stl
36.0 x 146.0 x 10.00

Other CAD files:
StartingGate/STL/starter_box/open-box.stl
FinishLine/STL/Track-4.stl
FinishLine/STL/Track-3.stl
StartingGate/STL/starter_box/sensor-track-flush.stl
FinishLine/STL/Track-2.stl
StartingGate/STL/starter_box/back-lid.stl
StartingGate/STL/starter_box/lane-2.stl
StartingGate/STL/starter_box/lane-4.stl
StartingGate/STL/starter_box/mount.stl
StartingGate/STL/starter_box/sensor-track.stl

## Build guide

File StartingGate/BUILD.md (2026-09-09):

# Diecast Remote Raceway - Starting Gate - Software Build Instructions

The simplest way to get started is to download the latest release as a complete 
Raspberry Pi system image for either the Raspberry Pi Zero W or the Raspberry
Pi Zero 2W.  These are complete images that can be burned to a microSD card
using the [Raspberry Pi Imager](https://www.raspberrypi.com/software/) or
[Balena Etcher](https://etcher.balena.io/)

## Building From Scratch

### Install Raspberry PI OS

The DRR software writes directly to the framebuffer and does not need a desktop OS image.

I recommend you install via the [Raspberry Pi Imager](https://www.raspberrypi.com/software/). You will need a minimum 8GB microSDHC card.
Insert the card into an appropriate card reader on your computer.

Run the Raspberry Pi Imager and select your board.

1.  On the "Device" tab either the "Raspberry Pi Zero W" or "Raspberry Pi Zerro 2 W" depending in which board you are using.  Click Next.
1.  On the "OS" tab select "Raspberry Pi OS (other)" then either "Raspberry Pi OS Lite (32-bit)" for the Zero or "Raspberry Pi Os
Lite (65-bit) for the Zero 2 board.  Click Next.
1.  On the "Storage" tab select the appropriate option for the storage card you are initializing. Click Next.
1.  On "Customization -> Hostname" tab enter the hostname for your Starting Gate.  I use "drr". Click Next.
1.  On "Customization -> Localisation" Specify your Country's capital, your Timezone and Keyboard Layout. Click Next.
1.  On "Customization -> User" Select a Username and Password. The prebuilt image uses "drr" and "HotWheels".  Click Next.
1.  On "Customization -> WiFi" Select a SSID and Password. The prebuilt image skips this step.  Click Next
1.  On "Customization -> Remote Access" Toggle the Enable SSH on and select "Use Password Authentication".  Click Next.
1.  On "Customization -> Raspberry Pi Connect" Set the toggle to Off.  Click Next
1.  Click on "WRITE" to write the OS image to your SD card

Once your SD card is initialized insert it into your Raspberry Pi Zero.
You can either connect a keyboard and monitor or just SSH into the device
when it boots. Log in using the username and password you created when
running the Raspberry Pi Imager.

Once logged in, I strongly recommend you upgrade any packages:

```
sudo apt update
sudo apt upgrade
```

### Install Python 3 and the necessary libraries

1. Install the necessary prerequisites:

    ```bash
    sudo apt install --no-install-recommends -y cmake git python3 python3-setuptools python3-dev python3-gpiozero python3-pigpio python3-bluez python3-pip libegl1-mesa-dev libgbm-dev libgles2-mesa-dev libdrm-dev
    ```

### Download Starting Gate Software from GitHub

At present, all three components (Starting Gate, Finish Line, Coordinator) are located in the same GitHub repository. Perform a sparse checkout to obtain just the Starting Gate directory.

```bash
wget https://raw.githubusercontent.com/tquiggle/Diecast-Remote-Raceway/refs/heads/master/StartingGate/util/git-sparse-checkout.sh

chmod +x git-sparse-checkout.sh
./git-sparse-checkout.sh
```

or execute the following by hand:

```bash
git clone --no-checkout https://github.com/tquiggle/Diecast-Remote-Raceway.git
cd Diecast-Remote-Raceway
git sparse-checkout init --cone
git sparse-checkout set StartingGate
git checkout
```

### Build and install pigpiod

Sadly, pigpiod is no longer available as a package from the standard RPI
repository as it doesn't support the Raspberry Pi 5. You need to build
it from source.

1.  Build pigpiod from source

```bash
wget https://github.com/joan2937/pigpio/archive/refs/tags/v79.tar.gz
tar zxf v79.tar.gz
cd pigpio-79
make
sudo make install

```

1.  Have pigpiod start on every boot and start it now (without having to reboot)

    Run the pigpiod-service.sh utility from the  utils subdirectory

    ```bash
    sudo ~/Diecast-Remote-Raceway/StartingGate/util/pigpiod-service.sh
    ```

### Setup the Waveshare 1.3" LCD HAT

Raspberry OS Bookworm has native support for the st7799 display driver chip.  There is no need to follow the instructions from the [Waveshare
Wiki](https://www.waveshare.com/wiki/1.3inch_LCD_HAT). The shell script `setup-waveshare-1.3-HAT.sh` in the util subdirectory will perform all necessary changes to a base Raspberry OS system.

```
sudo ~/Diecast-Remote-Raceway/StartingGate/util/setup-waveshare-1.3-HAT.sh
```

### Build the DRM version of Raylib

This mostly follows the instructions at the [Python Bindings for Raylib 5.5](https://electronstudio.github.io/raylib-python-cffi/README.html) Github page for [Compile Raylib from source DRM mode](https://electronstudio.github.io/raylib-python-cffi/RPI.html#option-3-compile-raylib-from-source-drm-mode) for the Raspberry Pi.

1. Build a shared lib version of Raylib in DRM mode and install to /usr:

    ```
    ~/Diecast-Remote-Raceway/StartingGate/util/build-raylib.sh
    ```

    ```
    git clone https://github.com/raysan5/raylib.git --branch 5.5 --single-branch
    cd raylib
    mkdir build
    cd build
    cmake -DPLATFORM="DRM" -DBUILD_EXAMPLES=OFF -DCUSTOMIZE_BUILD=ON -DSUPPORT_FILEFORMAT_JPG=ON -DSUPPORT_FILEFORMAT_FLAC=ON -DCMAKE_BUILD_TYPE=Release -DBUILD_SHARED_LIBS=ON -DCMAKE_INSTALL_PREFIX:PATH=/usr ..
    make -j
    sudo make install
    ```

1. Then have pip compile and install the wheel for the python bindings:

    ```
    sudo python3 -m pip install --break-system-packages setuptools
    sudo python3 -m pip install --break-system-packages --no-cache-dir --no-binary raylib --upgrade --force-reinstall raylib==5.5.0.0
    ```

That's it, you sould be able to run the DRR python application.

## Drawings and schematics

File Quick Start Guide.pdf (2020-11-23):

No Direct Sunlight | Reflective Car Bottom

1

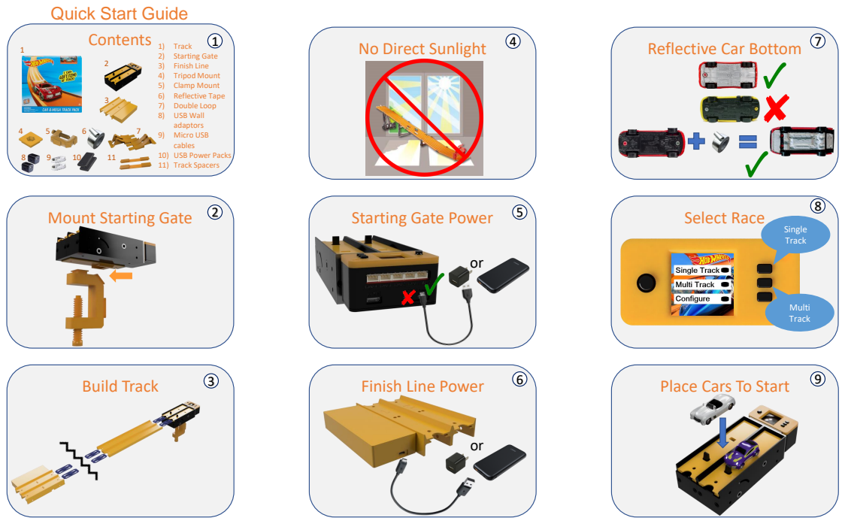
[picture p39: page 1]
Mount Starting Gate; Starting Gate Power; Select Race; Build Track; Place Cars To Start; Single Track; Multi Track

Quick Start Guide
Contents

1) Track
2) Starting Gate
3) Finish Line
4) Tripod Mount
5) Clamp Mount
6) Reflective Tape
7) Double Loop
8) USB Wall
adaptors
9) Micro USB
cables
10) USB Power Packs
11) Track Spacers

Finish Line Power

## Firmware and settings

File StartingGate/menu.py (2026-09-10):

#! /usr/bin/python3

"""
Diecast Remote Raceway - Menu

The menu hierarchy and associated enum values are described below.

My original thought was that I could intelligently use the enum values
in computing transitions while walking the hierarchy.  One digit values
representing top level menu items, two digit values representing second
level menu items, three digit values third level, etc.  This didn't
prove very useful.

The top level menu is treated special. Input is via one of the three
buttons on the right of the display.  The user can select from "Single
Track," "Multi Track" or "Configure" by just pressing the adjacent button
and the action is immediate.  If the user selects "Configure" they are
dumped into the various configuration options where navigation is done
using the joystick. Menu items are selected by pushing the joystick
button.  See the Input class for details on how text input is handled.

TODO:

   * Add menu item to select the name of the finish line to connect to

Logical Menu Layout:

    # __top_menu()
    * SINGLE_TRACK = 1
    * MULTI_TRACK = 2
    * CONFIGURE = 3
        # config_menu()
        * TRACK_NAME = 31
            * ENTER_TRACK_NAME = 311
        * NUM_LANES = 32
            * ENTER_NUM_LANES = 321
        * CAR_ICONS = 33
            # __car_menu()
            * CAR_1_ICON = 331
                * SELECT_CAR_1_ICON = 3311
            * CAR_2_ICON = 332
                * SELECT_CAR_2_ICON = 3321
            * CAR_3_ICON = 333
                * SELECT_CAR_3_ICON = 3331
            * CAR_4_ICON = 334
                * SELECT_CAR_4_ICON = 3341
        * CIRCUIT_NAME = 34
            * ENTER_CIRCUIT_NAME = 341
        * RACE_TIMEOUT = 35
            * ENTER_RACE_TIMEOUT = 351
        * WIFI_SETUP = 36
            # __wifi_menu()
            * WIFI_SSID = 361
                * ENTER_WIFI_SSID = 3611
            * WIFI_PSWD = 362
                * ENTER_WIFI_PSWD = 3621
            * WIFI_REGION = 363
                * ENTER_WIFI_REGION = 3631
        * COORDINATOR_SETUP = 37
            # __controller_menu()
            * COORD_HOSTNAME = 371
                * ENTER_COORD_HOSTNAME =3711
            * COORD_PORT = 372
                * ENTER_COORD_PORT =3721
        * SERVO_LIMITS = 38
            # __servo_menu
            * SERVO_DOWN_VALUE = 381
                * ENTER_SERVO_DOWN_VALUE = 3811
            * SERVO_UP_VALUE = 382
                * ENTER_SERVO_UP_VALUE = 3821
        * RESET_RESTART_SETUP = 39
            # __reset_restart_menu()
            * PERFORM_RESTART = 391
                * CONFIRM_RESTART = 3911
            * PERFORM_RESET = 392
                * CONFIRM_RESTART = 3921

Author: Tom Quiggle
tquiggle@gmail.com
https://github.com/tquiggle/Die-Cast-Remote-Raceway

Copyright (c) Thomas Quiggle. All rights reserved.

Licensed under the MIT license. See LICENSE file in the project root for full license information.
"""

import enum
import glob
import math
import os
import time

import pyray
from pyray import BLACK, LIGHTGRAY, ORANGE, RAYWHITE, WHITE, RED

from deviceio import DeviceIO, JOYU, JOYD, JOYL, JOYR, JOYP, SERVO
from input import Input, MODE_SPECIAL
from config import Config
from wifi import WiFi

@enum.unique
class MenuState(enum.Enum):
    """
    Enumerate all of the possible menu selection postions
    """
    # __top_menu()
    SINGLE_TRACK = 1
    MULTI_TRACK = 2
    CONFIGURE = 3
    # config_menu()
    TRACK_NAME = 31
    NUM_LANES = 32
    CAR_ICONS = 33
    CIRCUIT_NAME = 34
    RACE_TIMEOUT = 35
    WIFI_SETUP = 36
    COORDINATOR_SETUP = 37
    SERVO_LIMITS = 38
    RESET_RESTART_SETUP = 39
    # __car_menu()
    CAR_1_ICON = 331
    CAR_2_ICON = 332
    CAR_3_ICON = 333
    CAR_4_ICON = 334
    # __wifi_menu()
    WIFI_SSID = 361
    WIFI_PSWD = 362
    WIFI_REGION = 363
    # __controller_menu()
    COORD_HOSTNAME = 371
    COORD_PORT = 372
    # __servo_menu
    SERVO_DOWN_VALUE = 381
    SERVO_UP_VALUE = 382
    # __reset_restart_menu()
    PERFORM_RESTART = 391
    PERFORM_RESET = 392
    # Terminal entries in menu where we accept user input
    ENTER_TRACK_NAME = 311
    ENTER_NUM_LANES = 321
    SELECT_CAR_1_ICON = 3311
    SELECT_CAR_2_ICON = 3321
    SELECT_CAR_3_ICON = 3331
    SELECT_CAR_4_ICON = 3341
    ENTER_CIRCUIT_NAME = 341
    ENTER_RACE_TIMEOUT = 351
    ENTER_WIFI_SSID = 3611
    ENTER_WIFI_PSWD = 3621
    ENTER_WIFI_REGION = 3631
    ENTER_COORD_HOSTNAME = 3711
    ENTER_COORD_PORT = 3721
    ENTER_SERVO_DOWN_VALUE = 3811
    ENTER_SERVO_UP_VALUE = 3821
    CONFIRM_RESTART = 3911
    CONFIRM_RESET = 3921

    def next(self):
        """
        Returns next menu item in enum
        """
        cls = self.__class__
        members = list(cls)
        index = members.index(self) + 1
        if index >= len(members):
            index = 0
        return members[index]

    def prev(self):
        """
        Returns previous menu item in enum
        """
        cls = self.__class__
        members = list(cls)
        index = members.index(self) - 1
        index = max(index, 0)
        return members[index]

# Menu transitions when the joystick is pushed UP
UP = {}
UP[MenuState.SINGLE_TRACK] = MenuState.CONFIGURE
UP[MenuState.MULTI_TRACK] = MenuState.SINGLE_TRACK
UP[MenuState.CONFIGURE] = MenuState.MULTI_TRACK
UP[MenuState.TRACK_NAME] = MenuState.RESET_RESTART_SETUP
UP[MenuState.NUM_LANES] = MenuState.TRACK_NAME
UP[MenuState.CAR_ICONS] = MenuState.NUM_LANES
UP[MenuState.CAR_1_ICON] = MenuState.CAR_4_ICON
UP[MenuState.CAR_2_ICON] = MenuState.CAR_1_ICON
UP[MenuState.CAR_3_ICON] = MenuState.CAR_2_ICON
UP[MenuState.CAR_4_ICON] = MenuState.CAR_3_ICON
UP[MenuState.CIRCUIT_NAME] = MenuState.CAR_ICONS
UP[MenuState.RACE_TIMEOUT] = MenuState.CIRCUIT_NAME
UP[MenuState.WIFI_SETUP] = MenuState.RACE_TIMEOUT
UP[MenuState.WIFI_SSID] = MenuState.WIFI_REGION
UP[MenuState.WIFI_PSWD] = MenuState.WIFI_SSID
UP[MenuState.WIFI_REGION] = MenuState.WIFI_PSWD
UP[MenuState.COORDINATOR_SETUP] = MenuState.WIFI_SETUP
UP[MenuState.COORD_HOSTNAME] = MenuState.COORD_PORT
UP[MenuState.COORD_PORT] = MenuState.COORD_HOSTNAME
UP[MenuState.SERVO_LIMITS] = MenuState.COORDINATOR_SETUP
UP[MenuState.RESET_RESTART_SETUP] = MenuState.SERVO_LIMITS
UP[MenuState.PERFORM_RESET] = MenuState.PERFORM_RESTART
UP[MenuState.PERFORM_RESTART] = MenuState.PERFORM_RESET
UP[MenuState.SERVO_DOWN_VALUE] = MenuState.SERVO_UP_VALUE
UP[MenuState.SERVO_UP_VALUE] = MenuState.SERVO_DOWN_VALUE
UP[MenuState.ENTER_TRACK_NAME] = MenuState.ENTER_TRACK_NAME
UP[MenuState.ENTER_NUM_LANES] = MenuState.ENTER_NUM_LANES
UP[MenuState.ENTER_CIRCUIT_NAME] = MenuState.ENTER_CIRCUIT_NAME
UP[MenuState.ENTER_RACE_TIMEOUT] = MenuState.ENTER_RACE_TIMEOUT
UP[MenuState.ENTER_WIFI_SSID] = MenuState.ENTER_WIFI_SSID
UP[MenuState.ENTER_WIFI_PSWD] = MenuState.ENTER_WIFI_PSWD
UP[MenuState.ENTER_WIFI_REGION] = MenuState.ENTER_WIFI_REGION
UP[MenuState.ENTER_COORD_HOSTNAME] = MenuState.ENTER_COORD_HOSTNAME
UP[MenuState.ENTER_COORD_PORT] = MenuState.ENTER_COORD_PORT
UP[MenuState.ENTER_SERVO_UP_VALUE] = MenuState.ENTER_SERVO_UP_VALUE
UP[MenuState.ENTER_SERVO_DOWN_VALUE] = MenuState.ENTER_SERVO_DOWN_VALUE
UP[MenuState.SELECT_CAR_1_ICON] = MenuState.SELECT_CAR_1_ICON
UP[MenuState.SELECT_CAR_2_ICON] = MenuState.SELECT_CAR_2_ICON
UP[MenuState.SELECT_CAR_3_ICON] = MenuState.SELECT_CAR_3_ICON
UP[MenuState.SELECT_CAR_4_ICON] = MenuState.SELECT_CAR_4_ICON
UP[MenuState.CONFIRM_RESTART] = MenuState.CONFIRM_RESTART
UP[MenuState.CONFIRM_RESET] = MenuState.CONFIRM_RESET

# Menu transitions when the joystick is pushed DOWN
DOWN = {}
DOWN[MenuState.SINGLE_TRACK] = MenuState.MULTI_TRACK
DOWN[MenuState.MULTI_TRACK] = MenuState.CONFIGURE
DOWN[MenuState.CONFIGURE] = MenuState.SINGLE_TRACK

DOWN[MenuState.TRACK_NAME] = MenuState.NUM_LANES
DOWN[MenuState.NUM_LANES] = MenuState.CAR_ICONS
DOWN[MenuState.CAR_ICONS] = MenuState.CIRCUIT_NAME
DOWN[MenuState.CAR_1_ICON] = MenuState.CAR_2_ICON
DOWN[MenuState.CAR_2_ICON] = MenuState.CAR_3_ICON
DOWN[MenuState.CAR_3_ICON] = MenuState.CAR_4_ICON
DOWN[MenuState.CAR_4_ICON] = MenuState.CAR_1_ICON
DOWN[MenuState.CIRCUIT_NAME] = MenuState.RACE_TIMEOUT
DOWN[MenuState.RACE_TIMEOUT] = MenuState.WIFI_SETUP
DOWN[MenuState.WIFI_SETUP] = MenuState.COORDINATOR_SETUP
DOWN[MenuState.WIFI_SSID] = MenuState.WIFI_PSWD
DOWN[MenuState.WIFI_PSWD] = MenuState.WIFI_REGION
DOWN[MenuState.WIFI_REGION] = MenuState.WIFI_SSID
DOWN[MenuState.COORDINATOR_SETUP] = MenuState.SERVO_LIMITS
DOWN[MenuState.COORD_HOSTNAME] = MenuState.COORD_PORT
DOWN[MenuState.COORD_PORT] = MenuState.COORD_HOSTNAME
DOWN[MenuState.SERVO_LIMITS] = MenuState.RESET_RESTART_SETUP
DOWN[MenuState.SERVO_DOWN_VALUE] = MenuState.SERVO_UP_VALUE
DOWN[MenuState.SERVO_UP_VALUE] = MenuState.SERVO_DOWN_VALUE
DOWN[MenuState.RESET_RESTART_SETUP] = MenuState.TRACK_NAME
DOWN[MenuState.PERFORM_RESET] = MenuState.PERFORM_RESTART
DOWN[MenuState.PERFORM_RESTART] = MenuState.PERFORM_RESET
DOWN[MenuState.ENTER_TRACK_NAME] = MenuState.ENTER_TRACK_NAME
DOWN[MenuState.ENTER_NUM_LANES] = MenuState.ENTER_NUM_LANES
DOWN[MenuState.ENTER_CIRCUIT_NAME] = MenuState.ENTER_CIRCUIT_NAME
DOWN[MenuState.ENTER_RACE_TIMEOUT] = MenuState.ENTER_RACE_TIMEOUT
DOWN[MenuState.ENTER_WIFI_SSID] = MenuState.ENTER_WIFI_SSID
DOWN[MenuState.ENTER_WIFI_PSWD] = MenuState.ENTER_WIFI_PSWD
DOWN[MenuState.ENTER_WIFI_REGION] = MenuState.ENTER_WIFI_REGION
DOWN[MenuState.ENTER_COORD_HOSTNAME] = MenuState.ENTER_COORD_HOSTNAME
DOWN[MenuState.ENTER_SERVO_UP_VALUE] = MenuState.ENTER_SERVO_DOWN_VALUE
DOWN[MenuState.ENTER_SERVO_DOWN_VALUE] = MenuState.ENTER_SERVO_UP_VALUE
DOWN[MenuState.ENTER_COORD_PORT] = MenuState.ENTER_COORD_PORT
DOWN[MenuState.SELECT_CAR_1_ICON] = MenuState.SELECT_CAR_1_ICON
DOWN[MenuState.SELECT_CAR_2_ICON] = MenuState.SELECT_CAR_2_ICON
DOWN[MenuState.SELECT_CAR_3_ICON] = MenuState.SELECT_CAR_3_ICON
DOWN[MenuState.SELECT_CAR_4_ICON] = MenuState.SELECT_CAR_4_ICON
DOWN[MenuState.CONFIRM_RESTART] = MenuState.CONFIRM_RESTART
DOWN[MenuState.CONFIRM_RESET] = MenuState.CONFIRM_RESET

# Menu transitions when the joystick is pushed LEFT
LEFT = {}
LEFT[MenuState.SINGLE_TRACK] = MenuState.SINGLE_TRACK
LEFT[MenuState.MULTI_TRACK] = MenuState.MULTI_TRACK
LEFT[MenuState.CONFIGURE] = MenuState.CONFIGURE
LEFT[MenuState.TRACK_NAME] = MenuState.CONFIGURE
LEFT[MenuState.NUM_LANES] = MenuState.CONFIGURE
LEFT[MenuState.CAR_ICONS] = MenuState.CONFIGURE
LEFT[MenuState.CAR_1_ICON] = MenuState.CAR_ICONS
LEFT[MenuState.CAR_2_ICON] = MenuState.CAR_ICONS
LEFT[MenuState.CAR_3_ICON] = MenuState.CAR_ICONS
LEFT[MenuState.CAR_4_ICON] = MenuState.CAR_ICONS
LEFT[MenuState.CIRCUIT_NAME] = MenuState.CONFIGURE
LEFT[MenuState.RACE_TIMEOUT] = MenuState.CONFIGURE
LEFT[MenuState.WIFI_SETUP] = MenuState.CONFIGURE
LEFT[MenuState.WIFI_SSID] = MenuState.WIFI_SETUP
LEFT[MenuState.WIFI_PSWD] = MenuState.WIFI_SETUP
LEFT[MenuState.WIFI_REGION] = MenuState.WIFI_SETUP
LEFT[MenuState.COORDINATOR_SETUP] = MenuState.CONFIGURE
LEFT[MenuState.COORD_HOSTNAME] = MenuState.COORDINATOR_SETUP
LEFT[MenuState.COORD_PORT] = MenuState.COORDINATOR_SETUP
LEFT[MenuState.SERVO_LIMITS] = MenuState.CONFIGURE
LEFT[MenuState.SERVO_DOWN_VALUE] = MenuState.SERVO_LIMITS
LEFT[MenuState.SERVO_UP_VALUE] = MenuState.SERVO_LIMITS
LEFT[MenuState.RESET_RESTART_SETUP] = MenuState.CONFIGURE
LEFT[MenuState.PERFORM_RESET] = MenuState.RESET_RESTART_SETUP
LEFT[MenuState.PERFORM_RESTART] = MenuState.RESET_RESTART_SETUP
LEFT[MenuState.ENTER_TRACK_NAME] = MenuState.TRACK_NAME
LEFT[MenuState.ENTER_NUM_LANES] = MenuState.NUM_LANES
LEFT[MenuState.ENTER_CIRCUIT_NAME] = MenuState.CIRCUIT_NAME
LEFT[MenuState.ENTER_RACE_TIMEOUT] = MenuState.RACE_TIMEOUT
LEFT[MenuState.ENTER_WIFI_SSID] = MenuState.WIFI_SSID
LEFT[MenuState.ENTER_WIFI_PSWD] = MenuState.WIFI_PSWD
LEFT[MenuState.ENTER_WIFI_REGION] = MenuState.WIFI_REGION
LEFT[MenuState.ENTER_COORD_HOSTNAME] = MenuState.COORD_HOSTNAME
LEFT[MenuState.ENTER_COORD_PORT] = MenuState.COORD_PORT
LEFT[MenuState.ENTER_SERVO_UP_VALUE] = MenuState.SERVO_LIMITS
LEFT[MenuState.ENTER_SERVO_DOWN_VALUE] = MenuState.SERVO_LIMITS
LEFT[MenuState.SELECT_CAR_1_ICON] = MenuState.CAR_1_ICON
LEFT[MenuState.SELECT_CAR_2_ICON] = MenuState.CAR_2_ICON
LEFT[MenuState.SELECT_CAR_3_ICON] = MenuState.CAR_3_ICON
LEFT[MenuState.SELECT_CAR_4_ICON] = MenuState.CAR_4_ICON
LEFT[MenuState.CONFIRM_RESTART] = MenuState.CONFIRM_RESTART
LEFT[MenuState.CONFIRM_RESET] = MenuState.CONFIRM_RESET

# Menu transitions when the joystick button is pressed
SELECT = {}
SELECT[MenuState.SINGLE_TRACK] = MenuState.SINGLE_TRACK
SELECT[MenuState.MULTI_TRACK] = MenuState.MULTI_TRACK
SELECT[MenuState.CONFIGURE] = MenuState.TRACK_NAME
SELECT[MenuState.TRACK_NAME] = MenuState.ENTER_TRACK_NAME
SELECT[MenuState.NUM_LANES] = MenuState.ENTER_NUM_LANES
SELECT[MenuState.CAR_ICONS] = MenuState.CAR_1_ICON
SELECT[MenuState.CAR_1_ICON] = MenuState.SELECT_CAR_1_ICON
SELECT[MenuState.CAR_2_ICON] = MenuState.SELECT_CAR_2_ICON
SELECT[MenuState.CAR_3_ICON] = MenuState.SELECT_CAR_3_ICON
SELECT[MenuState.CAR_4_ICON] = MenuState.SELECT_CAR_4_ICON
SELECT[MenuState.CIRCUIT_NAME] = MenuState.ENTER_CIRCUIT_NAME
SELECT[MenuState.RACE_TIMEOUT] = MenuState.ENTER_RACE_TIMEOUT
SELECT[MenuState.WIFI_SETUP] = MenuState.WIFI_SSID
SELECT[MenuState.WIFI_SSID] = MenuState.ENTER_WIFI_SSID
SELECT[MenuState.WIFI_PSWD] = MenuState.ENTER_WIFI_PSWD
SELECT[MenuState.WIFI_REGION] = MenuState.ENTER_WIFI_REGION
SELECT[MenuState.COORDINATOR_SETUP] = MenuState.COORD_HOSTNAME
SELECT[MenuState.COORD_HOSTNAME] = MenuState.ENTER_COORD_HOSTNAME
SELECT[MenuState.COORD_PORT] = MenuState.ENTER_COORD_PORT
SELECT[MenuState.SERVO_LIMITS] = MenuState.SERVO_DOWN_VALUE
SELECT[MenuState.ENTER_TRACK_NAME] = MenuState.ENTER_TRACK_NAME
SELECT[MenuState.ENTER_NUM_LANES] = MenuState.ENTER_NUM_LANES
SELECT[MenuState.ENTER_CIRCUIT_NAME] = MenuState.ENTER_CIRCUIT_NAME
SELECT[MenuState.ENTER_RACE_TIMEOUT] = MenuState.ENTER_RACE_TIMEOUT
SELECT[MenuState.ENTER_WIFI_SSID] = MenuState.ENTER_WIFI_SSID
SELECT[MenuState.ENTER_WIFI_PSWD] = MenuState.ENTER_WIFI_PSWD
SELECT[MenuState.ENTER_COORD_HOSTNAME] = MenuState.ENTER_COORD_HOSTNAME
SELECT[MenuState.ENTER_COORD_PORT] = MenuState.ENTER_COORD_PORT
SELECT[MenuState.SERVO_DOWN_VALUE] = MenuState.ENTER_SERVO_DOWN_VALUE
SELECT[MenuState.SERVO_UP_VALUE] = MenuState.ENTER_SERVO_UP_VALUE
SELECT[MenuState.SELECT_CAR_1_ICON] = MenuState.SELECT_CAR_1_ICON
SELECT[MenuState.SELECT_CAR_2_ICON] = MenuState.SELECT_CAR_2_ICON
SELECT[MenuState.SELECT_CAR_3_ICON] = MenuState.SELECT_CAR_3_ICON
SELECT[MenuState.SELECT_CAR_4_ICON] = MenuState.SELECT_CAR_4_ICON
SELECT[MenuState.RESET_RESTART_SETUP] = MenuState.PERFORM_RESTART
SELECT[MenuState.PERFORM_RESTART] = MenuState.CONFIRM_RESTART
SELECT[MenuState.PERFORM_RESET] = MenuState.CONFIRM_RESET

# Text string displayed for each menu position
TEXT = {}
TEXT[MenuState.SINGLE_TRACK] = "Single Track"
TEXT[MenuState.MULTI_TRACK] = "Multi Track"
TEXT[MenuState.CONFIGURE] = "Configure"
TEXT[MenuState.TRACK_NAME] = "Track Name"
TEXT[MenuState.NUM_LANES] = "# of Lanes"
TEXT[MenuState.CAR_ICONS] = "Car Icons"
TEXT[MenuState.CAR_1_ICON] = "Car 1 Icon"
TEXT[MenuState.CAR_2_ICON] = "Car 2 Icon"
TEXT[MenuState.CAR_3_ICON] = "Car 3 Icon"
TEXT[MenuState.CAR_4_ICON] = "Car 4 Icon"
TEXT[MenuState.CIRCUIT_NAME] = "Circuit"
TEXT[MenuState.RACE_TIMEOUT] = "Race Timeout"
TEXT[MenuState.WIFI_SETUP] = "WiFi Setup"
TEXT[MenuState.WIFI_SSID] = "WiFi SSID"
TEXT[MenuState.WIFI_PSWD] = "WiFi Password"
TEXT[MenuState.WIFI_REGION] = "WiFi Region"
TEXT[MenuState.COORDINATOR_SETUP] = "Coordinator"
TEXT[MenuState.COORD_HOSTNAME] = "Coordinator Hostname"
TEXT[MenuState.COORD_PORT] = "Coordinator Port"
TEXT[MenuState.SERVO_LIMITS] = "Servo Limits"
TEXT[MenuState.SERVO_DOWN_VALUE] = "Servo Down Value"
TEXT[MenuState.SERVO_UP_VALUE] = "Servo Up Value"
TEXT[MenuState.RESET_RESTART_SETUP] = "Reset | Restart"

# Display function to call based on current menu position
FUNCTION = {}

class Menu:
    """
    This class implements the menu displayed at startup.  There is a single public
    method, process_menus(), to perform all menu operations.

    process_menus() updates the global config settings
    """

# PUBLIC

    def process_menus(self):
        """
        The main method that displays and walks the menu tree. The choice of
        SINGLE_TRACK vs MULTI_TRACK is set in the config.num_tracks

        The config is written back to disk if it was modified
        """

        print("process_menus: self=", self)
        self.race_type = None
        self.device.push_key_handlers(self.__key1, self.__key2, self.__key3, self.__joystick)
        while (not pyray.window_should_close()) and (self.race_type is None):
            if self.cursor_pos != self.last_cursor_pos:
                print("self.cursor_pos=", self.cursor_pos,
                      ", self.config_window_top=", self.config_window_top,
                      ", self.config_window_bottom=", self.config_window_bottom)
            pyray.begin_drawing()
            pyray.clear_background(RAYWHITE)
            pyray.draw_texture(self.background_texture, 0, 0, WHITE)
            self.last_cursor_pos = self.cursor_pos
            FUNCTION[self.cursor_pos]()
            if self.config_updated:
                self.config.save()
                self.config_updated = False
            pyray.end_drawing()
        self.device.pop_key_handlers()


    @staticmethod
    def break_string(text: str, max_len: int) -> list[str]:
        """
        Helper function shared with Display class.  Splits text into a list of
        strings each with a maximum length of max_len.
        """
        if not text:
            return []

        words = text.split()
        result = []
        current_chunk = []
        current_length = 0

        for word in words:
            word_len = len(word)
            # Check if adding the word exceeds max_len
            # Account for space between words if current_chunk is not empty
            extra = 1 if current_chunk else 0
            if current_length + word_len + extra > max_len and current_chunk:
                result.append(" ".join(current_chunk))
                current_chunk = [word]
                current_length = word_len
            else:
                current_chunk.append(word)
                current_length += word_len + extra

        if current_chunk:
            result.append(" ".join(current_chunk))

        return result
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

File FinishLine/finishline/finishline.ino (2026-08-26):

/*
  finish_line.ino

  The finish line is responsible for monitoring for cars passing over each lane
  and reporting back to the Starting Gate via Bluetooth.

  TODO(tq): Finish write-up including commands accepted over BlueTooth and OTA updates

Author: Tom Quiggle
tquiggle@gmail.com

https://github.com/tquiggle/Diecast-Remote-Raceway

Copyright (c) Thomas Quiggle. All rights reserved.

Licensed under the MIT license. See LICENSE file in the project root for 
full license information.


*/

#include <stddef.h>
#include <string>
#include <map>
#include <Base64.h>

#include "BluetoothSerial.h"

#if !defined(CONFIG_BT_ENABLED) || !defined(CONFIG_BLUEDROID_ENABLED)
#error Bluetooth is not enabled! Please run `make menuconfig` to and enable it
#endif

#include <Arduino.h>
#include <ArduinoJson.h>
#include <HTTPClient.h>
#include <HTTPUpdate.h>
#include <WiFiClient.h>
#include <WiFi.h>
#include <FS.h>
#include <SPIFFS.h>

#include "rsa_routines.h"


// Hard coded config
const char* FW_VERSION = "26082600";
// YYMMDDVV Last two digits of Year, Month, Day, Version
const char* configFilename = "/config.json";

// Adjust defaults as you see fit
#define URLLEN 100
#define DEFAULT_BT_ADVERTISEMENT "FinishLine"
#define MAX_CONFIG_SIZE 512
#define MAX_LANES 4
#define WIFI_CONNECT_MAX_TRYS 10

bool rsaInitialized = false;

// Configuration stored in config.json
String bluetoothAdvertisement(DEFAULT_BT_ADVERTISEMENT);

// Pin Assignments
const int LANE1_PIN = 16;
const int LANE2_PIN = 17;
const int LANE3_PIN = 18;
const int LANE4_PIN = 19;

enum Lanes {
  LANE1 = 0,  // Lanes is used as an array index
  LANE2,
  LANE3,
  LANE4
};

enum Commands {
  HELLO,
  RESTART,
  UPDATE_FW,
  BEGIN_RACE,
  END_RACE,
  VERSION,
  GET_PUBLIC_KEY,
  GET_CONFIG,
  SET_CONFIG,
  DELETE_CONFIG,
  UNKNOWN
};

#define DEBOUNCE_MILLIS 100
unsigned long lastFinish[MAX_LANES] = { 0, 0, 0, 0 };
const int finishMessageLength = 4;
const uint8_t* finishMessages[MAX_LANES] = {
  (uint8_t*)"FIN1",
  (uint8_t*)"FIN2",
  (uint8_t*)"FIN3",
  (uint8_t*)"FIN4"
};

/* Mapping for command string received over Bluetooth to enum */
static const std::map<String, Commands> commandTable = {
  { "HELO", Commands::HELLO },
  { "RSRT", Commands::RESTART },
  { "UPFW", Commands::UPDATE_FW },
  { "BGIN", Commands::BEGIN_RACE },
  { "ENDR", Commands::END_RACE },
  { "FLVS", Commands::VERSION },
  { "GKEY", Commands::GET_PUBLIC_KEY },
  { "GETC", Commands::GET_CONFIG },
  { "SETC", Commands::SET_CONFIG },
  { "DELC", Commands::DELETE_CONFIG }
};

Commands toCommand(String str) {
  std::map<String, Commands>::const_iterator iValue = commandTable.find(str);
  if (iValue == commandTable.end())
    return Commands::UNKNOWN;
  return iValue->second;
}

BluetoothSerial SerialBT;
bool raceRunning = false;

bool saveConfig(const char* filename) {
  if (!SPIFFS.begin(true)) {
    Serial.println("saveConfig(): SPIFFS.begin() failed.");
    return false;
  }

  if (SPIFFS.exists(filename)) {
    Serial.printf("saveConfig(): %s exists, removing.\n", filename);
    SPIFFS.remove(filename);
  }

  File config = SPIFFS.open(filename, FILE_WRITE);
  if (!config) {
    Serial.printf("saveConfig(): Failed to create config file %s\n", filename);
    return false;
  }

  JsonDocument doc;

  doc["bluetoothAdvertisement"] = bluetoothAdvertisement;

  String configJson;
  if (serializeJsonPretty(doc, configJson)) {
    Serial.printf("config = %s\n", configJson.c_str());
  }

  int bytesWritten = serializeJson(doc, config);
  Serial.printf("bytesWritten = %d\n", bytesWritten);

  if (bytesWritten <= 0)
    return false;

  config.close();
  SPIFFS.end();
  return true;
}

// Reads in the saved configuration from the SPIFFS file system on flash.
bool readConfig(const char* filename) {
  Serial.println("readConfig(): Compiled Defaults:");

  Serial.printf("  bluetoothAdvertisement = %s\n",
                bluetoothAdvertisement.c_str());

  if (!SPIFFS.begin(true)) {
    Serial.println("readConfig(): SPIFFS.begin() failed.");
    return false;
  }

  if (!SPIFFS.exists(filename)) {
    // Create config file with defaults
    Serial.printf("readConfig(): %s does not exist. Creating.\n", filename);
    saveConfig(filename);
    return true;
  }

  File config = SPIFFS.open(filename, FILE_READ);
  if (!config) {
    Serial.printf("readConfig(): unable to open %s\n", filename);
    return false;
  }

  JsonDocument doc;

  Serial.printf("readConfig(): calling deserializeJson\n");
  DeserializationError error = deserializeJson(doc, config);

  if (error) {
    Serial.printf("deserializeJson failed with code");
    Serial.println(error.f_str());
    Serial.printf("  unable to deserialize %s. Deleting.\n", filename);
    SPIFFS.remove(filename);
    return false;
  }

  Serial.printf("readConfig(): Configuration read from %s:\n", filename);
  serializeJson(doc, Serial);
  Serial.println("");

  if (doc["bluetoothAdvertisement"].is<String>()) {
    bluetoothAdvertisement = doc["bluetoothAdvertisement"].as<String>();
    Serial.print("  bluetoothAdvertisement = ");
    Serial.println(bluetoothAdvertisement);
  }

  Serial.printf("readConfig(): returning\n");
  config.close();
  SPIFFS.end();
  return true;
}

void deleteConfig(const char* filename) {
  Serial.println("deleteConfig():");

  if (!SPIFFS.begin(true)) {
    Serial.println("deleteConfig(): SPIFFS.begin() failed.");
    return;
  }
  SPIFFS.remove(filename);
  SPIFFS.end();
}

// Process a GETC command received via Bluetooth to update
bool getConfig(String configStr) {
  Serial.printf("getConfig(): configStr=%s\n", configStr);
  //StaticJsonDocument<MAX_CONFIG_SIZE> doc;
  JsonDocument doc;

  if (configStr.length() > 5) {
    String config = configStr.substring(5);
    Serial.printf("getConfig(): getting %s\n", config);
    if (configStr == "bluetoothAdvertisement") {
      doc["bluetoothAdvertisement"] = bluetoothAdvertisement;
    }
  } else {
    doc["bluetoothAdvertisement"] = bluetoothAdvertisement;
  }

  String configJson;
  if (serializeJsonPretty(doc, configJson)) {
    Serial.printf("config = %s\n", configJson.c_str());
  }
  SerialBT.write((const uint8_t*)configJson.c_str(), configJson.length());
  return true;
}

// Process a SETC command received via Bluetooth to update
bool setConfig(String configStr) {
  Serial.printf("setConfig(): configStr=%s\n", configStr.c_str());
  String key;
  String value;

  size_t pos = configStr.indexOf('=');
  if (pos > 0) {
    key = configStr.substring(0, pos);
    value = configStr.substring(pos + 1);
  } else {
    Serial.println("Invalid config string");
    return false;
  }

  Serial.printf("setConfig(): key=%s, value=%s\n", key.c_str(), value.c_str());
  if (key == "bluetoothAdvertisement") {
    bluetoothAdvertisement = value;
  } else {
    Serial.println("setConfig(): Invalid config name. Ignoring.");
    return false;
  }
  return saveConfig(configFilename);
}
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

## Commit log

2020-11-19 Initial check-in.
    [Controller-Box.stl, Controller-Lid.stl, Track-1.stl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]
2020-11-23 Added Quick Start Guide. Updated BOM with right-angle connectors.
2020-12-05 Implement remote config operations over Bluetooth. Fix bug constructing fwImageURL
    [finishline.ino]
2020-12-15 Added configs for servo limits. Alphabetized config constants and initialization.
2020-12-15 Correctly exchange track name and car icons during registration. Set Content-Type header.
    [coordinator.py]
2020-12-15 Revert to default SERVO init after switching from knock-off MG90S servos to real TowerPros.
    [deviceio.py]
2020-12-15 Cleaned up display transitions during race. Added logic to abort race on button push.
2020-12-15 Fix wifiPassword error in getConfig. Fixed mojibake in debug messages.
    [finishline.ino]
2021-01-09 Added support for setting servo up/down values
2021-01-11 Fix typeo in comment.
    [input.py]
2021-01-21 Disconnect servo when gate up. Abort on key press.
2021-01-24 Display "FAIL" for lanes that did not finish.
    [display.py]
2021-01-27 Skip update if unable to connect to server.
    [drr_wrapper.py]
2021-01-27 In main(), set remote track name after remote reg.
2022-07-01 Minor cleanup. Set remote track name before display when testing
2022-07-01 Avoid comparing version string to int return value
    [drr_wrapper.py]
2022-07-01 Reset race_type to none when redisplaying menu to avoid immediate exit
    [menu.py]
2022-07-01 Make MAX_Y private. Fix pylint error
    [display.py]
2022-07-01 Fix else after return style error
    [drr_wrapper.py]
2022-07-15 Disable Multi Track menu option of unable to communicate with Coordinator
2022-07-15 Fix minor pylint complaints
    [menu.py]
2024-08-10 Added custom PCB description and Gerber files
    [DRR HAT-B_Cu.gbr, DRR HAT-B_Mask.gbr, DRR HAT-B_Paste.gbr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]
